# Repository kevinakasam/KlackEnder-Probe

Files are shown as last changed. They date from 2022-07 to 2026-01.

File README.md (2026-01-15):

## KlackEnder Probe

KlackEnder Probe - **Simple, fast and cheap!**

<table>
  <tr>
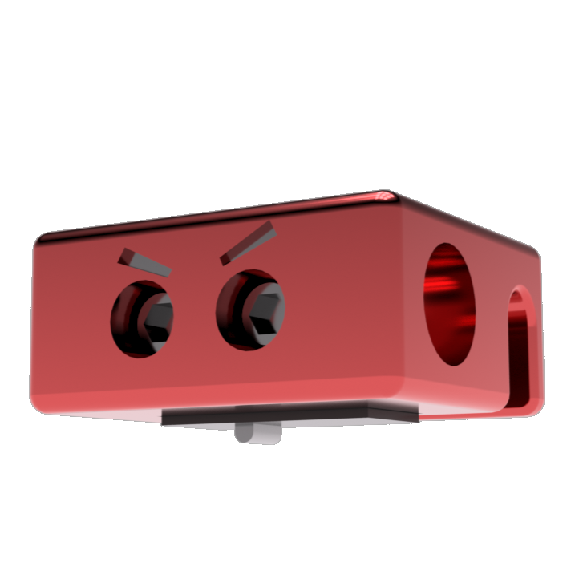
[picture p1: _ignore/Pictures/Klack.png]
    <td> </td>
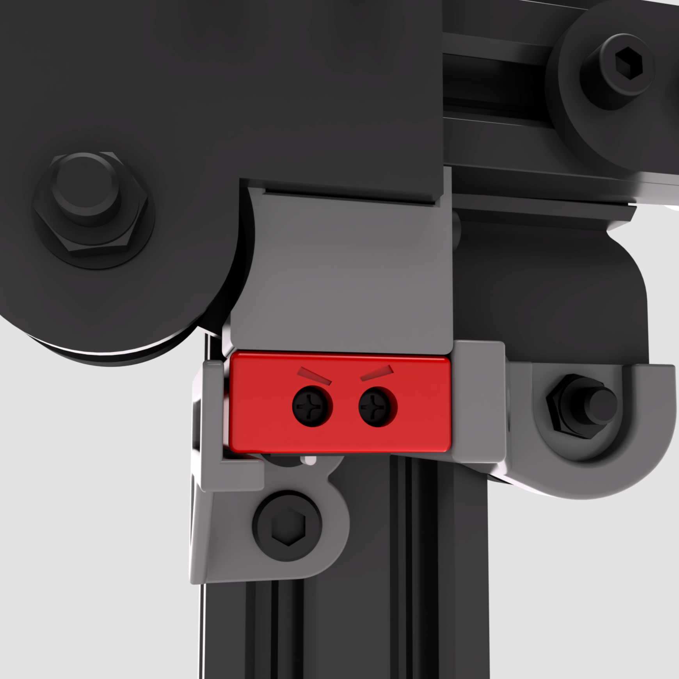
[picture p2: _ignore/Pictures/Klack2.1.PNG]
    <td> </td>
  </tr>
</table>

### What is this about?

Adaptation of the [Klicky](https://github.com/jlas1/Klicky-Probe)/[Quickdraw](https://github.com/Annex-Engineering/Quickdraw_Probe) Probe for the Ender 3 and comparable Creality printers. The probe is compatible with all printers that use the X plate of the Ender 3 and cost of the probe is <10€, of which the switch is the most expensive part.
The probe is compatible with Marlin and Klipper. Both firmwares work with the G29 command, the docking is done automatically by the printer, it couldn't be easier! Both firmwares add a KlackEnder menu to the display that can be used to dock and undock the Probe. The Bed-Mesh can be created via the custom menu, via the default firmware settings or with G29.

### Is it compatible with my printer?

As long as your printer uses a X-Axis plate that's similar to the one of the Ender 3: **YES!***
* You might have to adapt the parts (slightly) if you're not using an Ender 3 or the stock x-plate. See the Basic-Check section to check the basic measurements and see if you printer is compatible. If not and you really struggle with CAD just ping me on my [Discord](https://discord.gg/xqpKrxt9FC) ;)

### Why should I build it?

Well, as with my other mods, the focus is on the best cost-benefit ratio. The KlackEnder is very cheap and very easy to build. No need to pay 40-50€ for a probe that is still affected by heat, takes forever to mesh, and causes a lot of headaches to wire. For the Klack it's: Print - assemble - mount - start printing, that's it. Especially with Klipper, setup couldn't be easier, just use my pre-made macros, copy and paste, hit restart and you're ready for the next print.

#### Quick Overview:

- Compatible with Marlin and Klipper. Easy setup - firmware changes provided.
- 100% automatic probe docking and undocking.
- 100% open source parametric design! With the supported CAD file and instructions, it couldn't be easier to customize the parts to your needs! Even if you've never worked with CAD before, I promise you can customize the parts any way you want!
- Custom menu to control the probe (not for Ender 3 V2 with Jyers GUI).
- The cheapest way to get a fast and very accurate probing ( sample range of 1-2 microsteps (0.000-0.005mm with 16 microsteps)
- Easy to install, no soldering, no complicated wiring
- Works with all pressure surfaces, not affected by heat, no heat soak required

If you have any questions feel free to join the [Discord-Server](https://discord.gg/xqpKrxt9FC).
 
<a href="https://discord.gg/xqpKrxt9FC">
         <img alt="Join" src="https://github.com/kevinakasam/BeltDrivenEnder3/blob/main/_ignore/Pictures/Discord-Logo%2BWordmark-Color.png"
         width=250" >
</a>

<br>

### ❤️ Support my work

All my work is 100% Open-Source and free for everyone to use. But designing and developing all these mods takes a lot of time and effort, so if you appreciate my work and would like to support it and also help cover the costs of gettings the mods perfect, you can use one of the following links. Thanks a lot 🤍

<a href="https://www.buymeacoffee.com/kevinakasam" target="_blank">Buy Me A Coffee</a>


<br>

#### Parametric CAD Design

I always try my best to support a wide range of possible setups so you don't have to deal with CAD. With this design I have gone one step further: Not only does this design support a wide range of setups, but also the CAD is very easy to adapt for anyone, even if you've never worked with CAD before!

**How that? Parametric design!**

Parametric design means that everything is based on variables / parameters which you can easily change. The design itself adapts automatically to the changes you made. This may still sound a bit complicated, but trust me, with the detailed instructions I provide, it couldn't be easier! More about that on my [website](https://kevinakasam.com/lets-adapt-the-cad/).

## Bill of Materials + Instructions

As for my Belt-Mod, you can find all needed Hardware, STLs and instructions on my Website:

<a href="https://kevinakasam.com/klackender/">
         Guide
</a>

### STL-Files / Tolerances
<table>
  <tr>
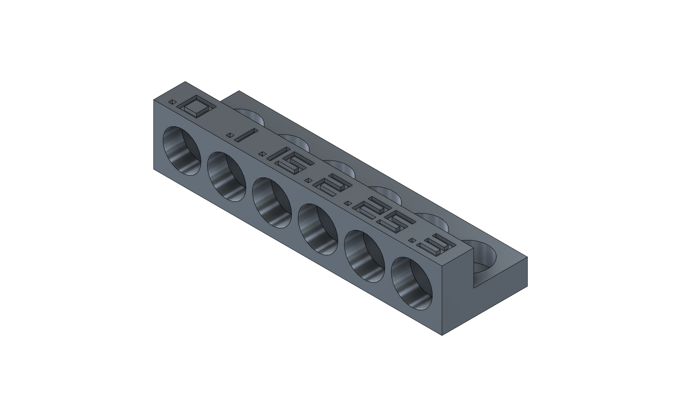
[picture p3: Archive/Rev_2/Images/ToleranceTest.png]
    <td> </td>
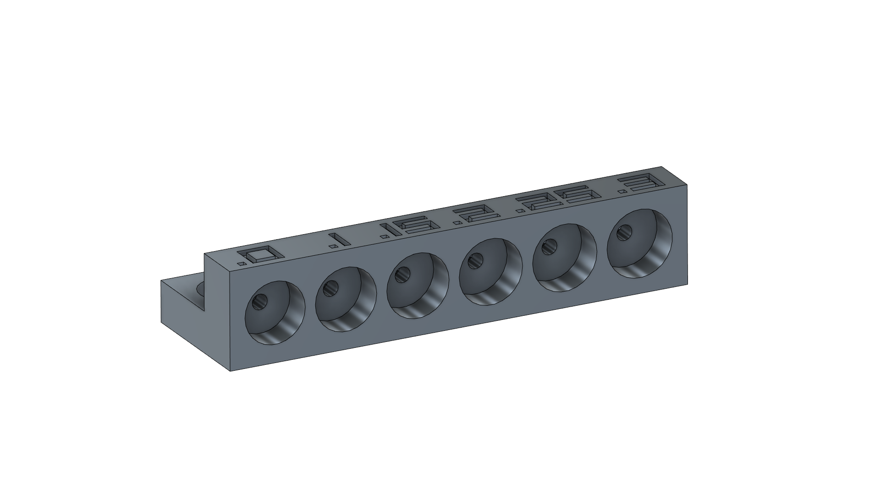
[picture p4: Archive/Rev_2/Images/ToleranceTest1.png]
    <td> </td>
  </tr>
</table>

Some people have contacted me with the problem that the layers split when they insert the magnets. This happens when the magnet is too big for the hole/the hole is too small for the magnet. So either the magnets are a bit bigger than 6mm or your printer prints the holes too small (never use a caliper to measure the magnets!. Only if they are made of plastic!). How the printer prints the holes depends not only on the material (ABS shrinks a bit, while PETG stays fairly constant) but also on the orientation of the holes. Vertical holes are usually a bit smaller than the horizontal ones, the ones that are printed in the walls. This is because these holes are formed by the layers and can never be completely round (the circle is made of 0.2mm (layer height) lines). At the same time, the diameter is strongly influenced by the print settings (speed, acceleration, linear advance/pressure advance, etc.).

However, you may need different tolerances than I do. That is why I have designed a small tolerance test (_thanks to SchlongkyDong for the idea!_). As already described, the tolerances for vertical and horizontal holes can/will differ. Stick a screwdriver through the smaller holes to get your magnets out again.

## Wiring Guide
Since there is no polarity on Switches, it doesn't matter which wire goes where. Just connect the switch to the two marked pins.
In the next chapter about firmware changes you will see where to add the pin.

Wiring for the Rev2 is very easy. Simply unmount/unplug your old z-endstop and connect the probe to the z-endstop port.

## Firmware Guide
The KlackEnder probe works with Marlin and Klipper. This guide only shows you what changes you need to make to the firmware, not how to modify/upload the firmware itself. There are several guides online for different boards and printers.
**You do not have to use the ```Probe In``` or ```Probe Out``` macros.** They're just a nice to have. The printer will do this automatically when you send a ```G29```.

### Klipper

The installation for Klipper is pretty easy. Simply do the changes below and copy the code from the ```KlackEnder.cfg```to your ```printer.cfg```
The ```[gcode_macro G29]``` does the same like the ```[gcode_macro BED_MESH_CALIBRATE]```. I just added this so you can use the G29 command as usual.
#### Changes to the existing config:
```
[stepper_z]
endstop_pin: probe:z_virtual_endstop #if you want to use the Prove as z-endstop (You can unsinstall the stock z endstop then. If not, remove the [homing_override])
#position_endstop: 0 #remove this or uncomment it with a #
position_min: -8 # set a negative value (minimum as the probe z_offset)

[stepper_x]
position_max: 250 #Your printhead have to move all the way to the right to pickup the probe. If your screw collides with the metal plate, simply flip it around.

##Following does not apply for the E3-V2##
[stepper_y]
position_min: READ #most Ender 3 configs have this wrong. Between the nozzle and the bed is a gap of 8mm (Y dimension) when the printer is homed. If not adapt this and the -8 in the Probe_In Makro (-5 for the Ender 3 Pro). 
position_endstop: SAME AS ABOVE

```
#### Config information:

**Add this DRIECTLY to your `printer.cfg` file:**
  ```
##################################
## Add this to your printer.cfg ##
##################################
#####################################################################
# KlackEnder- Settings
#####################################################################
[include KlackEnder.cfg]
# !! Change your Z endstop pin from 'endstop_pin: Pin123' to 'endstop_pin: probe:z_virtual_endstop'
# !! Also add in [stepper_y] 'position_min: -8'. Idk why but most configs have this wrong. For the Stock Ender 3 the homed Y position is -8.

[probe]
pin: ^YOUR_PIN #Change to where you plug your probe in, endstop or probe pin pulled high (^)
z_offset: 0 #Measure per your specific setup. Klipper will NOT save this value if this in not located in printer.cfg
x_offset: 4 # negative = left of the nozzle
y_offset: 21 # negative = in front of of the nozzle
speed: 5.0
lift_speed: 15.0
sample_retract_dist: 1
samples: 2
samples_tolerance_retries: 6

[bed_mesh]
speed: 300
horizontal_move_z: 5 #Positive value equal to z_offset or larger. eg: if z_offset is -2.5 this must be at least 2.5 or larger
mesh_min: 8,30
mesh_max: 223,201
probe_count: 5,5
#zero_reference_position: 117.5, 117.5 #for 235x235 bed. adapt to your bed size if needed. same for mesh min and max above
algorithm: bicubic
fade_start: 1
fade_end: 10
#fade_target:
#   The z position in which fade should converge. When this value is set
#   to a non-zero value it must be within the range of z-values in the mesh.
#   Users that wish to converge to the z homing position should set this to 0.
#   Default is the average z value of the mesh.
split_delta_z: 0.015
#   The amount of Z difference (in mm) along a move that will
#   trigger a split. Default is .025.
move_check_distance: 3
#   The distance (in mm) along a move to check for split_delta_z.
#   This is also the minimum length that a move can be split. Default
#   is 5.0.
mesh_pps: 4,4
#   A comma separated pair of integers (X,Y) defining the number of
#   points per segment to interpolate in the mesh along each axis. A
#   "segment" can be defined as the space between each probed
#   point. The user may enter a single value which will be applied
#   to both axes.  Default is 2,2.
#bicubic_tension: .2
#   When using the bicubic algorithm the tension parameter above
#   may be applied to change the amount of slope interpolated.
#   Larger numbers will increase the amount of slope, which
#   results in more curvature in the mesh. Default is .2.

[homing_override]
set_position_z:0 # Make printer think Z axis is at zero, so we can force a move upwards away from build plate
axes: z #will only call override if x is involved in the homing call
gcode:
    G90
    G1 Z10 F3000 ; move up to prevent accidentally scratching build plate    
    {% if "x" not in (printer.toolhead.homed_axes | lower) %}
        G28 X
    {% endif %}
    {% if "y" not in (printer.toolhead.homed_axes | lower) %}
        G28 Y        #Will only home XY if they are not currently homed
    {% endif %}
    PROBE_OUT
    G1 X113.5 Y96.5 F6000 ; Adjusted for normal klack offsets with a 235x235 bed X: 117.5 - x_offset, Y: 117.5 - y_offset
    G28 Z
    PROBE_IN
	
[screws_tilt_adjust] #Change to your specific printer is needed. Back left screw as referance point and that's where strain relief is is recommended
screw1: 28.5, 181.5
screw1_name: Back left
screw2: 28.5, 11.5
screw2_name: Front left
screw3: 198.5, 11.5
screw3_name: Front right
screw4: 198.5, 181.5
screw4_name: Back right
screw_thread: CW-M4 #Ender 3s use CW-M4 change for your printer if needed
horizontal_move_z: 10
# To calculate the position of your screws:
# Screw Offsets: 32.5mm for ender 3 beds
# Default Klack probe offsets: X: 4, Y: 21
#Back left	
#   X: 0 + screw_x_offset - probe.x_offset	
#   Y: 235 - screw_y_offset - probe.y_offset
#Front left	
#   X: 0 + screw_x_offset - probe.x_offset	
#   Y: 0 + screw_y_offset - probe.y_offset
#Front right 
#   X: 235 - screw_x_offset - probe.x_offset	
#   Y: 0 + screw_y_offset - probe.y_offset
#Back right	
#   X: 235 - screw_x_offset - probe.x_offset	
#   Y: 235 - screw_y_offset - probe.y_offset
# x and y offsets are usually the same. You will have to find info on your printer or measure them yourself
# This can be adapted for three screw bed as well without eny problem. In that case X offset of the third screw would be build volume divided by 2

[gcode_macro SCREWS_TILT_CALCULATE]
rename_existing: _SCREWS_TILT_CALCULATE
gcode:
    G28 ; Should always home before calculation even if already homed
    probe_out
    _SCREWS_TILT_CALCULATE
    probe_in
```
Add this section if building Dual Z. You can quickly comment and uncomment in Klipper by select the whole block and pressing Ctrl+/
```
##Uncomment for Dual Z setups only!! (with independent motors and drivers, not Y splitters nor dual Z port from one driver on board!)##
#[z_tilt]
#z_positions:
#    25,117
#    210,117
	#   A list of X, Y coordinates (one per line; subsequent lines
	#   indented) describing the location of each bed "pivot point". The
	#   "pivot point" is the point where the bed attaches to the given Z
	#   stepper. It is described using nozzle coordinates (the X, Y position
	#   of the nozzle if it could move directly above the point). The
	#   first entry corresponds to stepper_z, the second to stepper_z1,
	#   the third to stepper_z2, etc. This parameter must be provided.
#points:
#    4,96.5
#    219,96.5
	#   A list of X, Y coordinates (one per line; subsequent lines
	#   indented) that should be probed during a Z_TILT_ADJUST command.
	#   Specify coordinates of the nozzle and be sure the probe is above
	#   the bed at the given nozzle coordinates. This parameter must be
	#   provided.
#speed: 100
	#   The speed (in mm/s) of non-probing moves during the calibration.
	#   The default is 50.
#horizontal_move_z: 15
	#   The height (in mm) that the head should be commanded to move to
	#   just prior to starting a probe operation. The default is 5.
#retries: 10
	#   Number of times to retry if the probed points aren't within
	#   tolerance.
#retry_tolerance: 0.01
	#   If retries are enabled then retry if largest and smallest probed
	#   points differ more than retry_tolerance. Note the smallest unit of
	#   change here would be a single step. However if you are probing
	#   more points than steppers then you will likely have a fixed
	#   minimum value for the range of probed points which you can learn
	#   by observing command output.
	
#[gcode_macro Z_TILT_ADJUST] #Uncomment this macro if using dual z with z_tilt
#rename_existing: _Z_TILT_ADJUST
#gcode:
#    PROBE_OUT
#    _Z_TILT_ADJUST
#    PROBE_IN
```
Below are Macros and Screen menu settings to use with Klack. Add them in a seperate cfg called `KlackEnder.cfg`
```
#####################################################################
# KlackEnder- Macros
#####################################################################

[gcode_macro PROBE_OUT]
gcode:
    G90
    G1 X245 F4000
    G4 P300
    G1 Z15
    G1 X0

[gcode_macro PROBE_IN]
gcode:
    G90
    G1 Z20
    G1 X245 F12000
    G1 Y0 ; Check this against your config of [stepper_y] position_min: ...!
    G1 Z0
    G4 P300
    G1 X220 F6000
    G1 Z10
    G1 X0

[gcode_macro BED_MESH_CALIBRATE] #macro with parameter passing
rename_existing: _BED_MESH_CALIBRATE
gcode:
    PROBE_OUT
    _BED_MESH_CALIBRATE {rawparams}
    PROBE_IN

[gcode_macro G29] #reliant on the macro above
gcode:
    BED_MESH_CALIBRATE

[gcode_macro PROBE_CALIBRATE]
rename_existing: _PROBE_CALIBRATE
gcode:
    {% if not 'xyz' in printer.toolhead.homed_axes %}
    G28
    {% endif %}
    PROBE_OUT
    G90
    G1 Z20
    G1 X113.5 Y96.5 F12000 ; Readjust for center of bed adjusted for probe offset
    _PROBE_CALIBRATE
    TESTZ Z=20
    M117 Remove the Klack to continue calibration!

[gcode_macro PROBE_ACCURACY]
rename_existing: _PROBE_ACCURACY
gcode:
    {% if not 'xyz' in printer.toolhead.homed_axes %}
    G28
    {% endif %}
    PROBE_OUT
    G90
    G1 X113.5 Y96.5 F12000 ; Readjust for center of bed adjusted for probe offset
    _PROBE_ACCURACY
    PROBE_IN

#################################################################
#    KlackEnder- Menu - Only if you have a display installed!   #
# Will error if you don't have a display configured in klipper. #
#                       Remove if unneeded                      #
#################################################################

[menu __main]
type: list
name: Main

[menu __main __KlackEnder]
type: list
enable: True
name: KlackEnder

[menu __main __KlackEnder __ProbeOut]
type: command
name: Probe Out
gcode:
    PROBE_OUT

[menu __main __KlackEnder __ProbeIn]
type: command
name: Probe In
gcode:
    PROBE_IN

[menu __main __KlackEnder __AutoBedMesh]
type: command
name: Auto Bed Mesh
gcode:
    G28
    BED_MESH_CALIBRATE
	
[menu __main __KlackEnder __ScrewsTiltCalculate]
type: command
name: Screws Tilt Calculate
gcode:
    SCREWS_TILT_CALCULATE
  ```
### Kalico
If you are running the Kalico fork of Klipper you can use the `dockable_probe` feature in liu of the `probe` section and specific macros. Add to your `printer.cfg`.

```
[dockable_probe]
pin: ^YOUR_PIN #Change to where you plug your probe in, endstop or probe pin pulled high (^)
#z_offset: 0 #Measure per your specific setup
x_offset: 4 # negative = left of the nozzle
y_offset: 21 # negative = in front of of the nozzle
speed: 5.0
lift_speed: 10.0
sample_retract_dist: 2
samples: 3
samples_tolerance: 0.00625
samples_tolerance_retries: 6
#activate_gcode:
#deactivate_gcode:
drop_first_result: False #Make True if you have first probe inconsistancies

# Important Bits: These values may vary from printer to printer#
dock_position: 245,10 #Where the Klack is docked. ~X245 for v-wheel mount. ~X249 for Frank linear rail. Y value for clearance.
approach_position: 245,15 #same as dock_position for Euclid style probes
detach_position: 230,10,2 #Lower gantry to small Z pos to detach the probe
extract_position: 230,10 #Move that take the probe out of the dock
insert_position: 245,10 #same as dock_position for Euclid style probes

#safe_dock_distance :
#safe_position : approach_position
z_hop: 15.0 #This forces the toolhead up if not homed or moves the toolhead up to this value if already homed
restore_toolhead: True
#dock_retries:
auto_attach_detach: True
attach_speed:70
detach_speed:100
travel_speed:150
check_open_attach: True

[bed_mesh]
speed: 300
horizontal_move_z: 5 #Positive value equal to z_offset or larger. eg: if z_offset is -2.5 this must be at least 2.5 or larger
mesh_min: 8,30
mesh_max: 223,201
probe_count: 5,5
#zero_reference_position: 117.5, 117.5 #for 235x235 bed. adapt to your bed size if needed. same for mesh min and max above
algorithm: bicubic
fade_start: 1
fade_end: 10
#fade_target:
#   The z position in which fade should converge. When this value is set
#   to a non-zero value it must be within the range of z-values in the mesh.
#   Users that wish to converge to the z homing position should set this to 0.
#   Default is the average z value of the mesh.
split_delta_z: 0.015
#   The amount of Z difference (in mm) along a move that will
#   trigger a split. Default is .025.
move_check_distance: 3
#   The distance (in mm) along a move to check for split_delta_z.
#   This is also the minimum length that a move can be split. Default
#   is 5.0.
mesh_pps: 4,4
#   A comma separated pair of integers (X,Y) defining the number of
#   points per segment to interpolate in the mesh along each axis. A
#   "segment" can be defined as the space between each probed
#   point. The user may enter a single value which will be applied
#   to both axes.  Default is 2,2.
#bicubic_tension: .2
#   When using the bicubic algorithm the tension parameter above
#   may be applied to change the amount of slope interpolated.
#   Larger numbers will increase the amount of slope, which
#   results in more curvature in the mesh. Default is .2.
```
### Marlin
The installation for Marlin requires some more changes, but I will guide you through this :). These changes are only to get the KlackEnder working correctly. You still need to configure the rest of the options as appropriate for your printer. Support for the KlackEnder and similar probes was only recently added so a current version of Marlin needs to be used. Go to ```https://marlinfw.org/meta/download/``` and download the ```bugfix-2.1.x```. Follow the instructions for downloading, Installing, and configuring VSCode. Before compiling with PlatformIO you will need to setup your config files. Go to ```https://github.com/MarlinFirmware/Configurations/tree/bugfix-2.1.x/config/examples/Creality``` find your Printer/board setup and down load the appropriate Configuration.h & Configuration_adv.h. At this point you will want to go through and make the changes below, once completed you should be good to compile and use your printer. We are working on getting Configuration files posted for common printer combinations as well as .bins uploaded with pre-compiled firmware for common setups.

Marlin will now include a probe deploy and stow option under the motion menu when the Mag_mounted probe is defined.

#### 1. Configuration.h

- Search for ```//#define USE_PROBE_FOR_Z_HOMING``` and uncomment by removing ```//``` before ```#define```
- Search for ```#define PROBE_MANUALLY``` and if not commented out with ```//``` comment it out with ```//```
- If you have plugged your Probe into the Z-Endstop you will need to uncomment ```//#define Z_MIN_PROBE_USES_Z_MIN_ENDSTOP_PIN```
  If you have plugged your Probe into the probe port on your board you don't need to touch this.

- Search for ``` //#define MAG_MOUNTED_PROBE```  uncomment by removing the ```//```
  and change the following lines to
  ```
  #define MAG_MOUNTED_DEPLOY_1 { PROBE_DEPLOY_FEEDRATE, { 245, 114, 20 } }  // Move to side Dock / Attach probe
  #define MAG_MOUNTED_DEPLOY_2 { PROBE_DEPLOY_FEEDRATE, { 200, 114, 020} }  // Move probe off dock
  //#define MAG_MOUNTED_DEPLOY_3 { PROBE_DEPLOY_FEEDRATE, { 245, 114, 20 } }  // lift probe up
  //#define MAG_MOUNTED_DEPLOY_4 { PROBE_DEPLOY_FEEDRATE, {   0,   0,  0 } }  // Extra move if needed
  //#define MAG_MOUNTED_DEPLOY_5 { PROBE_DEPLOY_FEEDRATE, {   0,   0,  0 } }  // Extra move if needed
  #define MAG_MOUNTED_STOW_1   { PROBE_STOW_FEEDRATE,   { 245, 114, 20 } }  // Move to dock
  #define MAG_MOUNTED_STOW_2   { PROBE_STOW_FEEDRATE,   { 245, 114,  0 } }  // Place probe beside remover
  #define MAG_MOUNTED_STOW_3   { PROBE_STOW_FEEDRATE,   { 220, 114,  0 } }  // Side move to remove probe
  #define MAG_MOUNTED_STOW_4   { PROBE_STOW_FEEDRATE,   { 220, 114, 20 } }  // Ensure probe is off
  //#define MAG_MOUNTED_STOW_5   { PROBE_STOW_FEEDRATE,   {   0,   0,  0 } }  // Extra move if needed
  ```
  Probe deploy and stow feed rate can be changed by editing the appropriate lines

- Search for ```NOZZLE_TO_PROBE_OFFSET```  and change
  ```
  #define NOZZLE_TO_PROBE_OFFSET { 10, 10, 0 }

  // Most probes should stay away from the edges of the bed, but
  // with NOZZLE_AS_PROBE this can be negative for a wider probing area.
  #define PROBING_MARGIN 10
  ```

  to

  ```
  #define NOZZLE_TO_PROBE_OFFSET { 8, 21, 1.2 }   //--> set correct offset

  // Most probes should stay away from the edges of the bed, but
  // with NOZZLE_AS_PROBE this can be negative for a wider probing area.
  #define PROBING_MARGIN 15   //--> more clearance to the sides of the bed.
  ```
 
- Search for ```// @section geometry```  and change
  ```
  // The size of the printable area
  #define X_BED_SIZE 200
  #define Y_BED_SIZE 200

  // Travel limits (mm) after homing, corresponding to endstop positions.
  #define X_MIN_POS 0
  #define Y_MIN_POS 0
  #define Z_MIN_POS 0
  #define X_MAX_POS X_BED_SIZE
  #define Y_MAX_POS Y_BED_SIZE
  #define Z_MAX_POS 200
  ```

  For non Ender 3v2's

  ```
  // The size of the printable area
  #define X_BED_SIZE 230    //--> adjust bed size
  #define Y_BED_SIZE 235    //--> adjust bed size

  // Travel limits (mm) after homing, corresponding to endstop positions.
  #define X_MIN_POS 0
  #define Y_MIN_POS -8     //--> adjust endstop position
  #define Z_MIN_POS 0
  #define X_MAX_POS X_BED_SIZE +15     //--> adjust x travel
  #define Y_MAX_POS Y_BED_SIZE
  #define Z_MAX_POS 250     //--> adjust z travel
  ```
  For Ender 3v2's change it to
    ```
  // The size of the printable area
  #define X_BED_SIZE 230    //--> adjust bed size
  #define Y_BED_SIZE 228    //--> adjust bed size

  // Travel limits (mm) after homing, corresponding to endstop positions.
  #define X_MIN_POS 0
  #define Y_MIN_POS 0     //--> adjust endstop position
  #define Z_MIN_POS 0
  #define X_MAX_POS X_BED_SIZE +15     //--> adjust x travel
  #define Y_MAX_POS Y_BED_SIZE
  #define Z_MAX_POS 250     //--> adjust z travel
  ```
 
- Search for ```// @section calibrate```  and change
  ```
  //#define AUTO_BED_LEVELING_3POINT
  //#define AUTO_BED_LEVELING_LINEAR
  //#define AUTO_BED_LEVELING_BILINEAR
  //#define AUTO_BED_LEVELING_UBL
  //#define MESH_BED_LEVELING

  /**
  * Normally G28 leaves leveling disabled on completion. Enable one of
  * these options to restore the prior leveling state or to always enable
  * leveling immediately after G28.
  */
  //#define RESTORE_LEVELING_AFTER_G28
  //#define ENABLE_LEVELING_AFTER_G28
  ```

  to

  ```
  //#define AUTO_BED_LEVELING_3POINT
  //#define AUTO_BED_LEVELING_LINEAR
  //#define AUTO_BED_LEVELING_BILINEAR
  #define AUTO_BED_LEVELING_UBL     //--> Remove //
  //#define MESH_BED_LEVELING

  /**
  * Normally G28 leaves leveling disabled on completion. Enable one of
  * these options to restore the prior leveling state or to always enable
  * leveling immediately after G28.
  */
  #define RESTORE_LEVELING_AFTER_G28    //--> Remove //
  //#define ENABLE_LEVELING_AFTER_G28
  ```
 
- Search for ```Unified Bed Leveling```  
  Change  from ```#define MESH_INSET 1``` to ```#define MESH_INSET 10```
  Change   ```#define GRID_MAX_POINTS_X 10``` to ```#define GRID_MAX_POINTS_X 15```  
  Uncomment  by removing the ```//``` before ```#define UBL_MESH_WIZARD```  
  Uncomment  ```//#define LCD_BED_LEVELING```  
  Uncomment  ```//#define LCD_BED_TRAMMING```  
  Uncomment  ```//#define BED_TRAMMING_USE_PROBE```  
  Uncomment  ```//#define Z_SAFE_HOMING```  
  Uncomment  ```//#define EEPROM_INIT_NOW   // Init EEPROM on first boot after a new build```  

 - In Configuration_adv.H
  Uncomment ```//#define PROBE_OFFSET_WIZARD```

  ## Marlin Setup Before printing
  Go into the menu->Motion->Unified Bed Leveling->UBL Custom Bed Mesh
  set your normal bed temp and hotend temp and then select custom mesh. This will probe all points that can be reached by the probe and then interpolate the rest.
  
  ## Marlin Slicer Start Gcode
  In your slicer Gcode look for a line that says 
  ```G28```
  after that line add in the following two lines
  ```
  G29 L0 ; load mesh saved in slot 0 which is the default slot
  G29 A ; activate bed mesh leveling.
  G29 J ; Probe 3 points and tilt the mesh loaded in slot 0 to match the current bed tilt
  ```

### Rev_1 vs. Rev_2 (and Rev_2.x)

What's the difference between Revision 1 and Revion 2?
                   
The most important difference is the position of the probe. With the Rev2, the probe is attached to the X-axis, which is why the probe can be used as a Z end stop. So no additional port for an end stop is needed and the probe can simply be connected to the old Z endstop port. The renders below show the difference, the upper one is the Rev2. (The Probe mount on the hotendplate is the same for both version)
                   
<table>
  <tr>
    <td><img src="https://github.com/kevinakasam/KlackEnder-Probe/blob/main/Archive/Rev_2/Images/Comp.png" width="450"> </td>
    <td><img src="https://github.com/kevinakasam/KlackEnder-Probe/blob/main/Archive/Rev_2/Images/Comp2.png" width="450"> </td>
  </tr>
</table>

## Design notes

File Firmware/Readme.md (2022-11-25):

Firmware files for the KlackEnder.
See Wiring Guide and Firmware Guide from the main Readme.md for more information.

Marlin instructions are on the main Page!

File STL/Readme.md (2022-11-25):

All parts can be printed without supports. Just print them in the provided orientation.

**Print the tolerance test first!**
All horizontal holes have a tolerance of 0.2mm, all vertical ones have no tolerance. This should fit most printers and give you a tight fit. If the fit isn't right use the provided CAD files to change the tolerance. The f3d file has paramters for that (Check out my [website](https://kevinakasam.com/lets-adapt-the-cad/)). You could also join the discord and I will send you a file with the tolerances you want.

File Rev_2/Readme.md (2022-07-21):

## KlackEnder Probe *Revision 2*

KlackEnder Probe - **Simple, fast and cheap!**
  
Adaptation of the [Klicky](https://github.com/jlas1/Klicky-Probe)/[Quickdraw](https://github.com/Annex-Engineering/Quickdraw_Probe) Probe for the Ender 3 and comparable         Creality printers. The probe is compatible with all printers that use the X plate of the Ender 3. The cost of the probe is <5€, of which the switch is the most expensive part.
The probe is compatible with **Marlin and Klipper**. Both firmwares work with the G29 command, the docking is done automatically by the printer, it couldn't be easier! Both    firmwares add a KlackEnder menu to the display that can be used to dock and undock the Probe. The Bed-Mesh can be created via the custom menu, via the default firmware settings or with G29.

**With the Rev2 you can replace the stock limit switch with the probe. This means you don't need an additional endstop port like for the Rev1.**

### Quick Overview:
- Compatible with Marlin and Klipper. Firmware is provided.
- Automatic docking and undocking of the probe.
- Custom menu to control the probe.
- Cheap way to get fast and accurate probing.
- Easy to install, no soldering.
- Works with all print surfaces
- **Use it as Z Endstop with the Rev2**

Its working very well for me. If you have any questions feel free to join the [Discord-Server](https://discord.gg/xqpKrxt9FC) 
 
<a href="https://discord.gg/xqpKrxt9FC">
         <img alt="Join" src="https://github.com/kevinakasam/BeltDrivenEnder3/blob/main/Pictures/Discord-Logo%2BWordmark-Color.png"
         width=250" >
      </a>

<table>
  <tr>
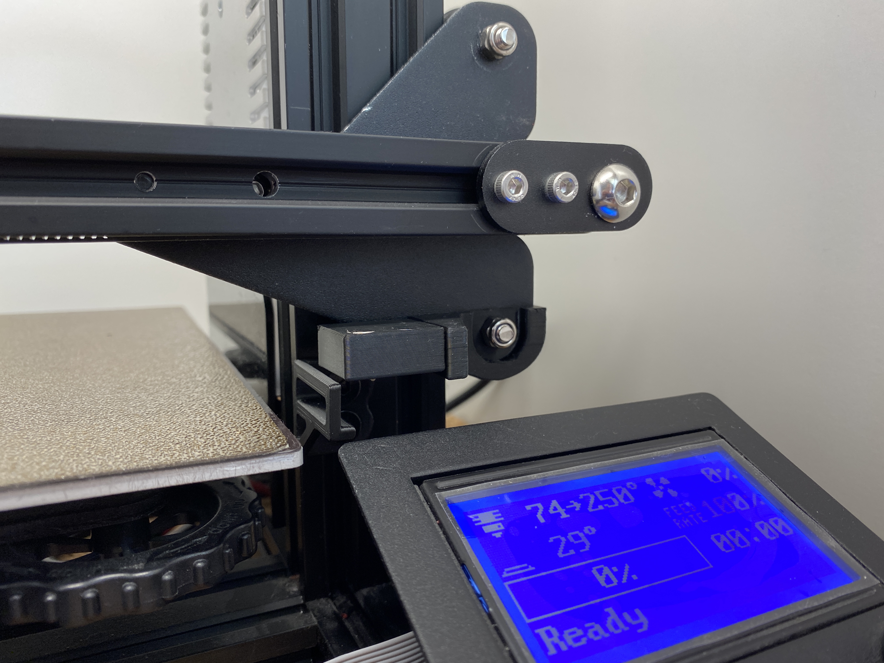
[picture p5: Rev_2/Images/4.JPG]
    <td> </td>
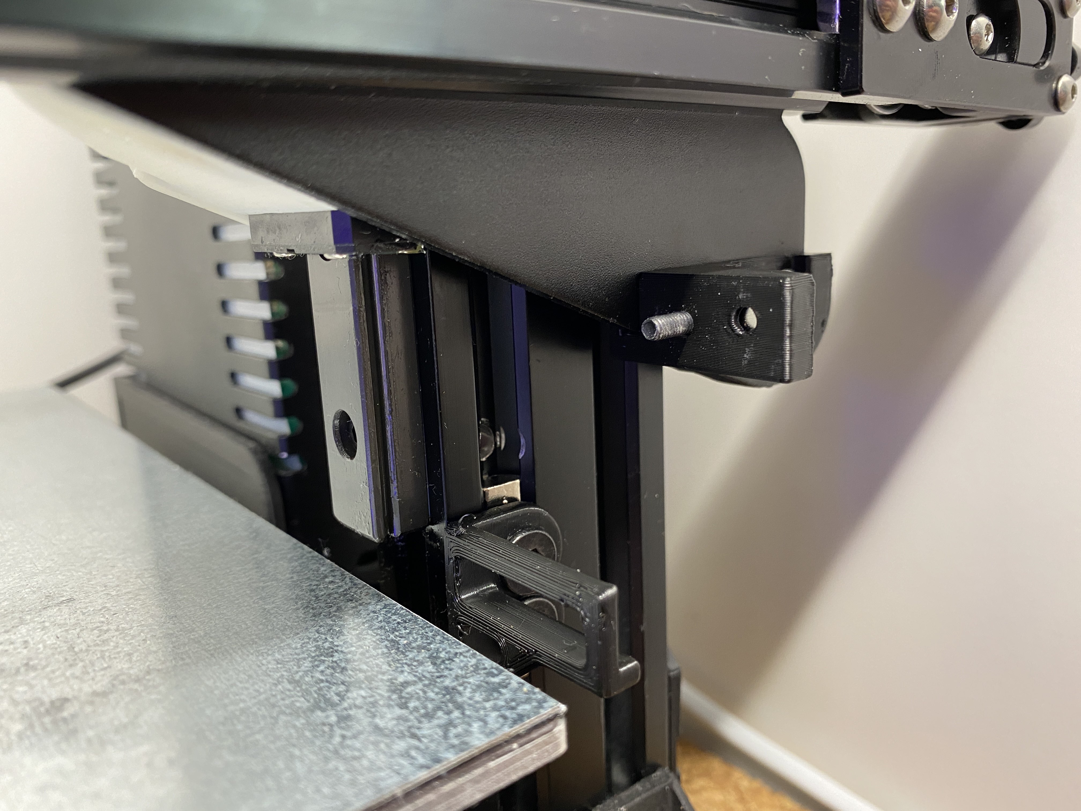
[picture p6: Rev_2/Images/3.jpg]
    <td> </td>
  </tr>
</table>

### BOM - Parts you need:
- 1x OMRON D2F or similar switch
- 6x Magnet 3x6mm 
- 1x M3x12-22mm screw (SHCS or BHCS doesn't matter)
- 2x M5x8mm screw (SHCS or BHCS doesn't matter)
- 2x M5 t-nut
- small zip tie and some cable (you may also need a connector to connect the probe to the mainboard e.g JST XH)
- Users of the Belt Z Mod: 1x M5x45mm screw (SHCS or BHCS doesn't matter) (with the wheels the 40mm screw is just long enough, for the MGN it's too short)
                                                                                                              
## STL-Files / Tolerances
<table>
  <tr>
    <td> </td>
    <td> </td>
  </tr>
</table>

Some people have contacted me with the problem that the layers split when they insert the magnets. This happens when the magnet is too big for the hole/the hole is too small for the magnet. So either the magnets are a bit bigger than 6mm or your printer prints the holes too small (never use a caliper to measure the magnets!. Only if they are made of plastic!). How the printer prints the holes depends not only on the material (ABS shrinks a bit, while PETG stays fairly constant) but also on the orientation of the holes. Vertical holes are usually a bit smaller than the horizontal ones, the ones that are printed in the walls. This is because these holes are formed by the layers and can never be completely round (the circle is made of 0.2mm (layer height) lines). At the same time, the diameter is strongly influenced by the print settings (speed, acceleration, linear advance/pressure advance, etc.).

However, you may need different tolerances than I do. That is why I have designed a small tolerance test (_thanks to SchlongkyDong for the idea!_). As already described, the tolerances for vertical and horizontal holes can/will differ. Stick a screwdriver through the smaller holes to get your magnets out again.

### Parametric Fusion 360 File
There is an f3d file in the [CAD](https://github.com/kevinakasam/KlackEnder-Probe/tree/main/Rev_2/CAD) folder. This file format is for Autodesk Fusion 360, a free CAD program for private users. You can use it to adjust the tolerances if the STL files I provided do not fit.
As described in the tolerance test, there are different tolerances for vertical and horizontal holes. Follow the steps decribes in the [CAD](https://github.com/kevinakasam/KlackEnder-Probe/tree/main/Rev_2/CAD) folder to create your own STL.

## Assembly Guide
                                                                                                               
I will add a Video Guide soon! The assembly is very similar to the Rev1. You will have to insert an additinal magnet into the side of the `Probe_Block.stl`. There also belongs a magnet in the foremost hole of `Probe_Dock.stl` (looking at it when it's mounted). The M3 scew belongs into the rear hole (the thread will stick out of the dock and hold the Proble_Block in place.
                                                                                                               
                                                                                                               
---

## Wiring Guide
Since there is no polarity on Swichtes, it doesn't matter which wire goes where. Just connect the switch to the two marked pins.
In the next chapter about firmware changes you will see where to add the pin.

Wiring for the Rev2 is very easy. Simply unmount/unplug your old z-endstop and connect the probe to the z-endstop port.

## Firmware Guide
The KlackEnder probe works with Marlin and Klipper. This guide only shows you what changes you need to make to the firmware, not how to modify/upload the firmware itself. There are several guides online for different boards and printers.
**You do not have to use the ```Probe In``` or ```Probe Out``` macros.** They're just a nice to have. The printer will do this automatically when you send a ```G29```.

### Klipper

The installation for Klipper is pretty easy. Simply copy the code from the ```KlackEnder.cfg```to your ```printer.cfg```
The ```[gcode_macro G29]``` does the same like the ```[gcode_macro AUTO_BED_MESH]```. I just added this so you can use the G29 commend as usual.

**Don't forgot to edit your probe Pin:**
  ```
  ##################################
## Add this to your printer.cfg ##
################################## 
#####################################################################
#	KlackEnder- Settings
#####################################################################

# !! Change your Z endstop pin from 'endstop_pin: Pin123' to 'endstop_pin: probe:z_virtual_endstop'
# !! Also add in [stepper_y] 'position_min: -8'. Idk why but most configs mave this wrong. For the Stock Ender 3 the homed Y position is -8.

[probe]
pin: ^PC14 #Probe-Stop Connection on Skr Mini Pro V1.2
z_offset: -2 #Measure per your specific setup
x_offset: 8 # negative = left of the nozzle
y_offset: 21 # negative = in front of of the nozzle
speed: 5.0
lift_speed: 15.0
sample_retract_dist: 1
samples: 2
samples_tolerance_retries: 6

##[(7x7)-1] / 2 = 24
##[(5x5)-1] / 2 = 12
[bed_mesh]
speed: 300
horizontal_move_z: 2
mesh_min: 8,30
mesh_max: 223,201
probe_count: 5,5
relative_reference_index: 12
algorithm: bicubic
fade_start: 1
fade_end: 10
#fade_target:
#   The z position in which fade should converge. When this value is set
#   to a non-zero value it must be within the range of z-values in the mesh.
#   Users that wish to converge to the z homing position should set this to 0.
#   Default is the average z value of the mesh.
split_delta_z: 0.015
#   The amount of Z difference (in mm) along a move that will
#   trigger a split. Default is .025.
move_check_distance: 3
#   The distance (in mm) along a move to check for split_delta_z.
#   This is also the minimum length that a move can be split. Default
#   is 5.0.
mesh_pps: 4,4
#   A comma separated pair of integers (X,Y) defining the number of
#   points per segment to interpolate in the mesh along each axis. A
#   "segment" can be defined as the space between each probed
#   point. The user may enter a single value which will be applied
#   to both axes.  Default is 2,2.
#bicubic_tension: .2
#   When using the bicubic algorithm the tension parameter above
#   may be applied to change the amount of slope interpolated.
#   Larger numbers will increase the amount of slope, which
#   results in more curvature in the mesh. Default is .2.

[homing_override]
set_position_z:0 # Make printer think Z axis is at zero, so we can force a move upwards away from build plate
gcode:
    G90
    G1 Z10 F3000 ; move up to prevent accidentally scratching build plate    
    G28 X
    G28 Y
    PROBE_OUT
    G1 X117 Y117 F6000
    G28 Z
    PROBE_IN

##For Dual Z setups only!! (with indipendent motors, no Y splitters or dual Z port on board!)##
[z_tilt]
z_positions:
    0,117
    235,117
#   A list of X, Y coordinates (one per line; subsequent lines
#   indented) describing the location of each bed "pivot point". The
#   "pivot point" is the point where the bed attaches to the given Z
#   stepper. It is described using nozzle coordinates (the X, Y position
#   of the nozzle if it could move directly above the point). The
#   first entry corresponds to stepper_z, the second to stepper_z1,
#   the third to stepper_z2, etc. This parameter must be provided.
points:
    8,96.5
    215,96.5
#   A list of X, Y coordinates (one per line; subsequent lines
#   indented) that should be probed during a Z_TILT_ADJUST command.
#   Specify coordinates of the nozzle and be sure the probe is above
#   the bed at the given nozzle coordinates. This parameter must be
#   provided.
speed: 300
#   The speed (in mm/s) of non-probing moves during the calibration.
#   The default is 50.
horizontal_move_z: 15
#   The height (in mm) that the head should be commanded to move to
#   just prior to starting a probe operation. The default is 5.
retries: 10
#   Number of times to retry if the probed points aren't within
#   tolerance.
retry_tolerance: 0.01
#   If retries are enabled then retry if largest and smallest probed
#   points differ more than retry_tolerance. Note the smallest unit of
#   change here would be a single step. However if you are probing
#   more points than steppers then you will likely have a fixed
#   minimum value for the range of probed points which you can learn
#   by observing command output.

#####################################################################
#	KlackEnder- Macros
#####################################################################

[gcode_macro PROBE_OUT]
gcode:
    G90
    G1 X245 F4000
    G4 P300
    G1 Z15
    G1 X0

[gcode_macro PROBE_IN]
gcode:
    G90
    G1 Z20
    G1 X245 F20000
    G1 Y-8
    G1 Z0
    G4 P300
    G1 X220 F6000
    G1 Z10
    G1 X0

[gcode_macro AUTO_BED_MESH]
gcode:
    PROBE_OUT
    BED_MESH_CALIBRATE
    #G1 Y0 F20000
    PROBE_IN

[gcode_macro G29]
gcode:
    PROBE_OUT
    BED_MESH_CALIBRATE
    #G1 Y0 F20000
    PROBE_IN

[gcode_macro Accuracy_Test]
gcode:
    PROBE_OUT
    G90
    G1 Y120 X120 F20000
    PROBE_ACCURACY
    PROBE_IN

[gcode_macro AUTO_Z_TILT_ADJUST]
gcode:
    PROBE_OUT
    Z_TILT_ADJUST
    PROBE_IN

#####################################################################
#	KlackEnder- Menu
#####################################################################

[menu __main]
type: list
name: Main

[menu __main __KlackEnder]
type: list
enable: True
name: KlackEnder

[menu __main __KlackEnder __ProbeOut]
type: command
name: Probe Out
gcode:
    PROBE_OUT

[menu __main __KlackEnder __ProbeIn]
type: command
name: Probe In
gcode:
    PROBE_IN

[menu __main __KlackEnder __AutoBedMesh]
type: command
name: Auto Bed Mesh
gcode:
    G28
    AUTO_BED_MESH
  ```

### Marlin
The installation for Marlin requires some more changes, but I will guide you through this :). These changes are only to get the KlackEnder working correctly. You still need to configure the rest of the options as appropriate for your printer. Support for the KlackEnder and similar probes was only recently added so a current version of Marlin needs to be used. Go to ```https://marlinfw.org/meta/download/``` and download the ```2.1.x.zip```. Follow the instructions for downloading, Installing, and configuring VSCode. Before compiling with PlatformIO you will need to setup your config files. Go to ```https://github.com/MarlinFirmware/Configurations/tree/bugfix-2.1.x/config/examples/Creality``` find your Printer/board setup and down load the appropriate Configuration.h & Configuration_adv.h. At this point you will want to go through and make the changes below, once completed you should be good to compile and use your printer. We are working on getting Configuration files posted for common printer combinations as well as .bins uploaded with pre-compiled firmeware for common setups.

Marlin will now include a probe deploy and stow option under the motion menu when the Mag_mounted probe is defined.

#### 1. Configuration.h
- Search for ``` #define Z_MIN_PROBE_USES_Z_MIN_ENDSTOP_PIN``` (line 1244) comment out by adding ```//``` before ```#define```

- Search for ```//#define USE_PROBE_FOR_Z_HOMING``` and uncomment by remvoving ```//``` before ```#define```

- Search for ``` //#define MAG_MOUNTED_PROBE``` (line 1349) uncomment by removing the ```//```
  and change lines 1354-1363 to 
  ```
  #define MAG_MOUNTED_DEPLOY_1 { PROBE_DEPLOY_FEEDRATE, { 245, 114, 20 } }  // Move to side Dock / Attach probe
  #define MAG_MOUNTED_DEPLOY_2 { PROBE_DEPLOY_FEEDRATE, { 200, 114, 020} }  // Move probe off dock
  //#define MAG_MOUNTED_DEPLOY_3 { PROBE_DEPLOY_FEEDRATE, { 245, 114, 20 } }  // lift probe up
  //#define MAG_MOUNTED_DEPLOY_4 { PROBE_DEPLOY_FEEDRATE, {   0,   0,  0 } }  // Extra move if needed
  //#define MAG_MOUNTED_DEPLOY_5 { PROBE_DEPLOY_FEEDRATE, {   0,   0,  0 } }  // Extra move if needed
  #define MAG_MOUNTED_STOW_1   { PROBE_STOW_FEEDRATE,   { 245, 114, 20 } }  // Move to dock
  #define MAG_MOUNTED_STOW_2   { PROBE_STOW_FEEDRATE,   { 245, 114,  0 } }  // Place probe beside remover
  #define MAG_MOUNTED_STOW_3   { PROBE_STOW_FEEDRATE,   { 240, 114,  0 } }  // Side move to remove probe
  #define MAG_MOUNTED_STOW_4   { PROBE_STOW_FEEDRATE,   { 240, 114, 20 } }  // Ensure probe is off
  //#define MAG_MOUNTED_STOW_5   { PROBE_STOW_FEEDRATE,   {   0,   0,  0 } }  // Extra move if needed
  ```
  Probe deploy and stow feedrate can be changed by edditing line's 1351-1352

- Search for ```NOZZLE_TO_PROBE_OFFSET``` (line 1453) and change
  ```
  #define NOZZLE_TO_PROBE_OFFSET { 10, 10, 0 }

  // Most probes should stay away from the edges of the bed, but
  // with NOZZLE_AS_PROBE this can be negative for a wider probing area.
  #define PROBING_MARGIN 10
  ```

  to 

  ```
  #define NOZZLE_TO_PROBE_OFFSET { 8, 21, 1.2 }   --> set correct offset

  // Most probes should stay away from the edges of the bed, but
  // with NOZZLE_AS_PROBE this can be negative for a wider probing area.
  #define PROBING_MARGIN 15   --> more clearance to the sides of the bed.
  ```
  
- Search for ```// @section machine``` (line 1661) and change
  ```
  // The size of the printable area
  #define X_BED_SIZE 200
  #define Y_BED_SIZE 200

  // Travel limits (mm) after homing, corresponding to endstop positions.
  #define X_MIN_POS 0
  #define Y_MIN_POS 0
  #define Z_MIN_POS 0
  #define X_MAX_POS X_BED_SIZE
  #define Y_MAX_POS Y_BED_SIZE
  #define Z_MAX_POS 200
  ```

  to 

  ```
  // The size of the printable area
  #define X_BED_SIZE 230    --> adjust bed size
  #define Y_BED_SIZE 235    --> adjust bed size

  // Travel limits (mm) after homing, corresponding to endstop positions.
  #define X_MIN_POS 0
  #define Y_MIN_POS -8      --> adjust endstop position
  #define Z_MIN_POS 0
  #define X_MAX_POS +15     --> adjust x travel
  #define Y_MAX_POS Y_BED_SIZE
  #define Z_MAX_POS 250     --> adjust z travel
  ```
  
- Search for ```// @section calibrate``` (line 1806) and change
  ```
  //#define AUTO_BED_LEVELING_3POINT
  //#define AUTO_BED_LEVELING_LINEAR
  //#define AUTO_BED_LEVELING_BILINEAR
  //#define AUTO_BED_LEVELING_UBL
  //#define MESH_BED_LEVELING

  /**
  * Normally G28 leaves leveling disabled on completion. Enable one of
  * these options to restore the prior leveling state or to always enable
  * leveling immediately after G28.
  */
  //#define RESTORE_LEVELING_AFTER_G28
  //#define ENABLE_LEVELING_AFTER_G28
  ```

  to 

  ```
  //#define AUTO_BED_LEVELING_3POINT
  //#define AUTO_BED_LEVELING_LINEAR
  //#define AUTO_BED_LEVELING_BILINEAR
  #define AUTO_BED_LEVELING_UBL     --> Remove //
  //#define MESH_BED_LEVELING

  /**
  * Normally G28 leaves leveling disabled on completion. Enable one of
  * these options to restore the prior leveling state or to always enable
  * leveling immediately after G28.
  */
  #define RESTORE_LEVELING_AFTER_G28    --> Remove //
  //#define ENABLE_LEVELING_AFTER_G28
  ```
  
- Search for ```Unified Bed Leveling``` line(1937)
  Change line 1942 from ```#define MESH_INSET 1```
  to ```#define MESH_INSET 10```
  
  Change line 1943 from ```#define GRID_MAX_POINTS_X 10```  
  to ```#define GRID_MAX_POINTS_X 15```  
  Uncomment line 1954 by removing the ```//``` before ```#define UBL_MESH_WIZARD```  
  Uncomment line 1974 ```//#define LCD_BED_LEVELING```  
  Uncomment Line 1983 ```//#define LCD_BED_TRAMMING```  
  Uncomment Line 1990 ```//#define BED_TRAMMING_USE_PROBE```  
  Uncomment Line 2048 ```//#define Z_SAFE_HOMING```
  Uncomment Line 2138 ```//#define EEPROM_INIT_NOW   // Init EEPROM on first boot after a new build```

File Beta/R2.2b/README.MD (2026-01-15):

Klack R2.2 Beta notes:

Overview:
- New smaller probe block and dock changes!
- Hexagonal holes for the magnets!
- No need to clip the middle lead anymore and leads bend down under the magnets in the block.

BoM Changes:
- No longer need the M3x12-16mm screw for teh dock.

Offset Changes:
- X: Stays the same
- Y: Subtract 2mm

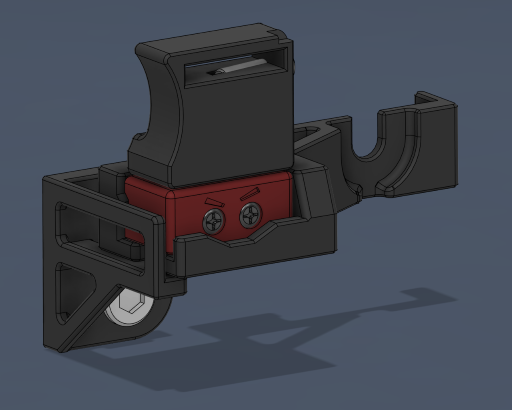
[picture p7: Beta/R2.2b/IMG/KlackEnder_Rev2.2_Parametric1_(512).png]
Klack Rev2.2


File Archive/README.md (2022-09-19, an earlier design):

## KlackEnder Probe

KlackEnder Probe - **Simple, fast and cheap!**
  
Adaptation of the [Klicky](https://github.com/jlas1/Klicky-Probe)/[Quickdraw](https://github.com/Annex-Engineering/Quickdraw_Probe) Probe for the Ender 3 and comparable         Creality printers. The probe is compatible with all printers that use the X plate of the Ender 3. The cost of the probe is <5€, of which the switch is the most expensive part.
The probe is compatible with **Marlin and Klipper**. Both firmwares work with the G29 command, the docking is done automatically by the printer, it couldn't be easier! Both    firmwares add a KlackEnder menu to the display that can be used to dock and undock the Probe. The Bed-Mesh can be created via the custom menu, via the default formware settings or with G29.

I recommend to use the Rev2!

### Quick Overview:
- Compatible with Marlin and Klipper. Firmware is provided.
- Automatic docking and undocking of the probe.
- Custom menu to control the probe.
- Cheap way to get fast and accurate probing.
- Easy to install, no soldering.
- Works with all print surfaces
- **Use it as Z Endstop with the Rev2**

Its working very well for me. If you have any questions feel free to join the [Discord-Server](https://discord.gg/xqpKrxt9FC) 
 
<a href="https://discord.gg/xqpKrxt9FC">
         <img alt="Join" src="https://github.com/kevinakasam/BeltDrivenEnder3/blob/main/_ignore/Pictures/Discord-Logo%2BWordmark-Color.png"
         width=250" >
</a>

### Rev_1 vs. Rev_2
What's the difference between Revision 1 and Revion 2?
                   
The most important difference is the position of the probe. With the Rev2, the probe is attached to the X-axis, which is why the probe can be used as a Z end stop. So no additional port for an end stop is needed and the probe can simply be connected to the old Z endstop port. The renders below show the difference, the upper one is the Rev2. (The Probe mount on the hotendplate is the same for both version)
                   
<table>
  <tr>
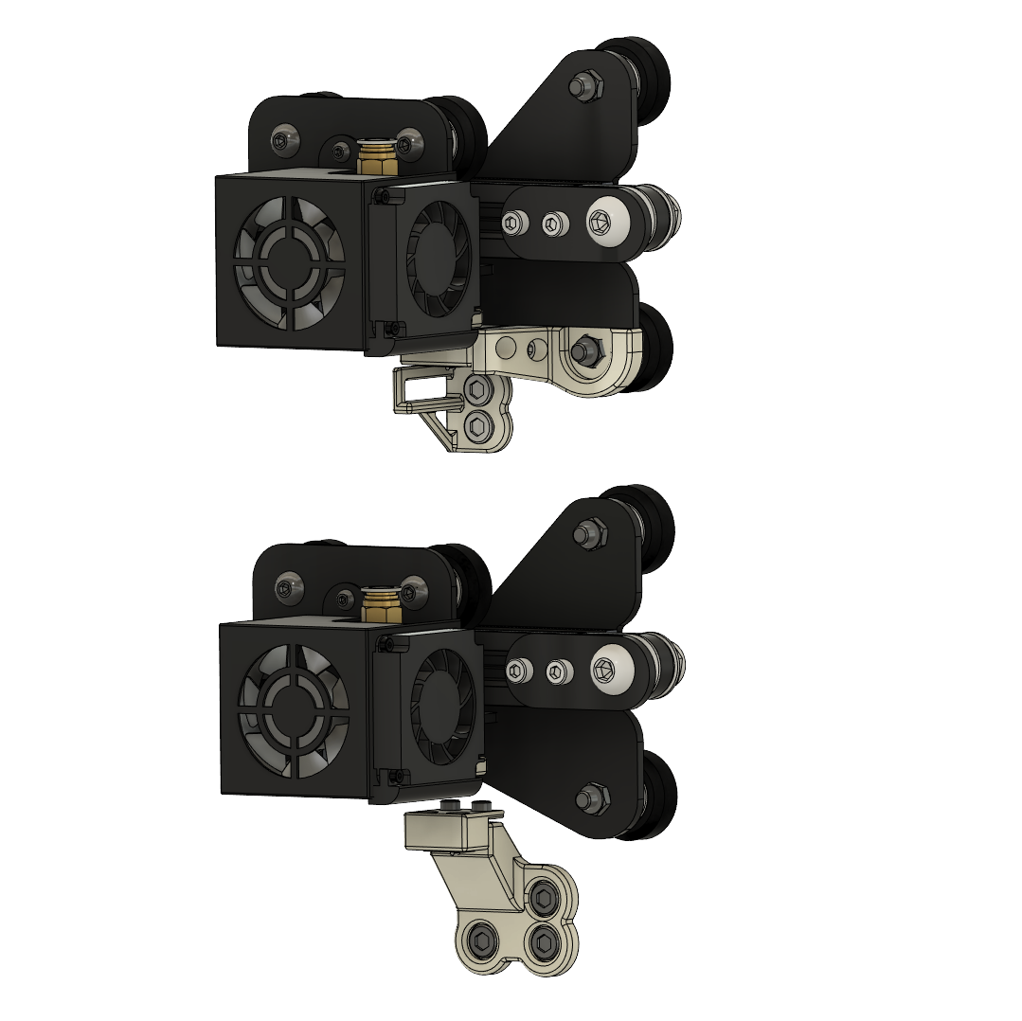
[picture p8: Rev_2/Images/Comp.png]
    <td> </td>
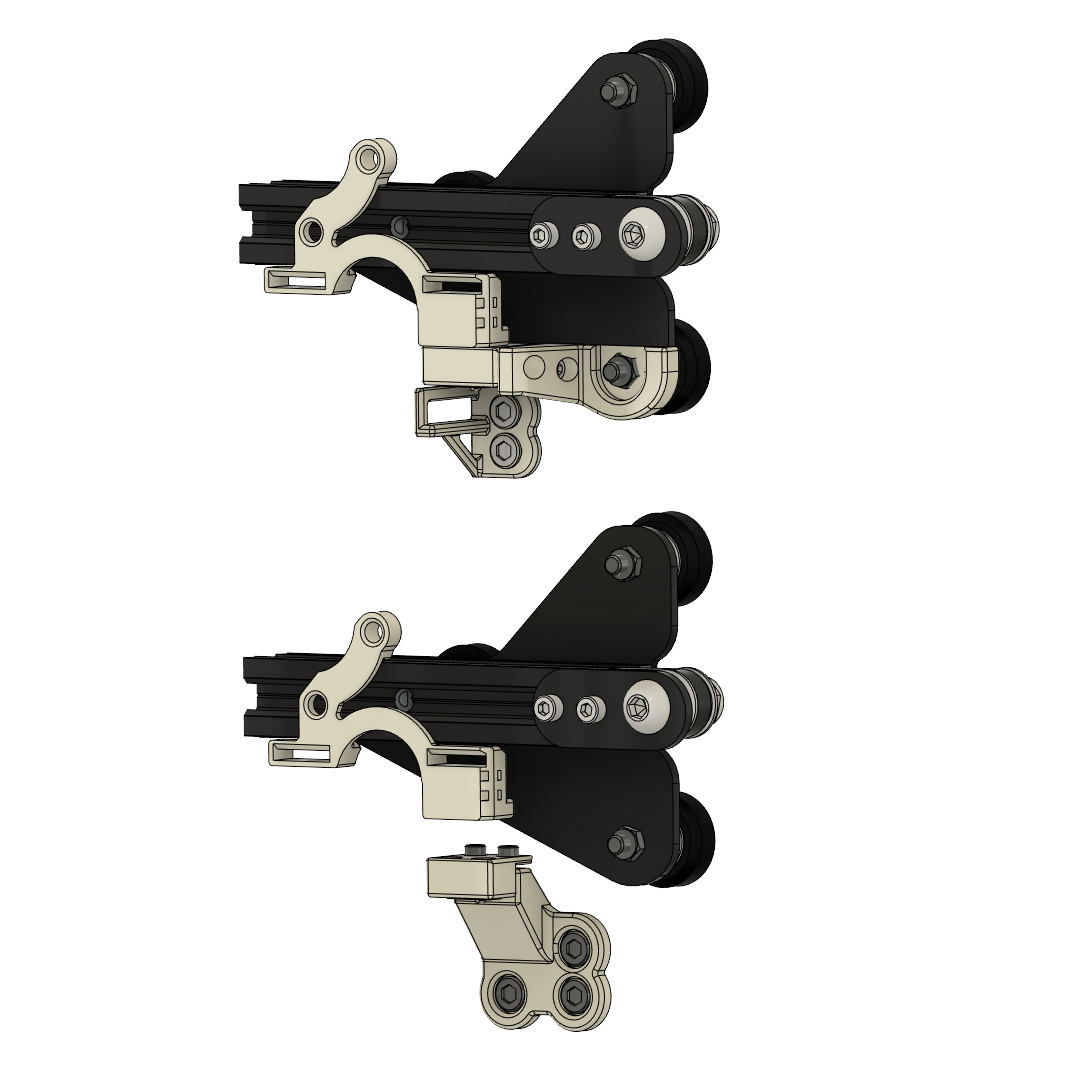
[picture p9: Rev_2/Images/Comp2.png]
    <td> </td>
  </tr>
</table>

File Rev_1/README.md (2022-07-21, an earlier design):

## KlackEnder Probe *Revision 1*

KlackEnder Probe - **Simple, fast and cheap!**
  
Adaptation of the [Klicky](https://github.com/jlas1/Klicky-Probe)/[Quickdraw](https://github.com/Annex-Engineering/Quickdraw_Probe) Probe for the Ender 3 and comparable         Creality printers. The probe is compatible with all printers that use the X plate of the Ender 3. The cost of the probe is <5€, of which the switch is the most expensive part.
The probe is compatible with **Marlin and Klipper**. Both firmwares work with the G29 command, the docking is done automatically by the printer, it couldn't be easier! Both    firmwares add a KlackEnder menu to the display that can be used to dock and undock the Probe. The Bed-Mesh can be created via the custom menu, via the default formware settings or with G29. **Important note: You have to set the offset to the z limit switch, not to the probe! The printer calculates the first layer from the z endstops position and the probed mesh!**

### Quick Overview:
- Compatible with Marlin and Klipper. Firmware is provided.
- Automatic docking and undocking of the probe.
- Custom menu to control the probe.
- Cheap way to get fast and accurate probing.
- Easy to install, no soldering.
- Works with all print surfaces

Its working very well for me. If you have any questions feel free to join the [Discord-Server](https://discord.gg/xqpKrxt9FC) 
 
<a href="https://discord.gg/xqpKrxt9FC">
         <img alt="Join" src="https://github.com/kevinakasam/BeltDrivenEnder3/blob/main/Pictures/Discord-Logo%2BWordmark-Color.png"
         width=250" >
      </a>

<table>
  <tr>
    <td> </td>
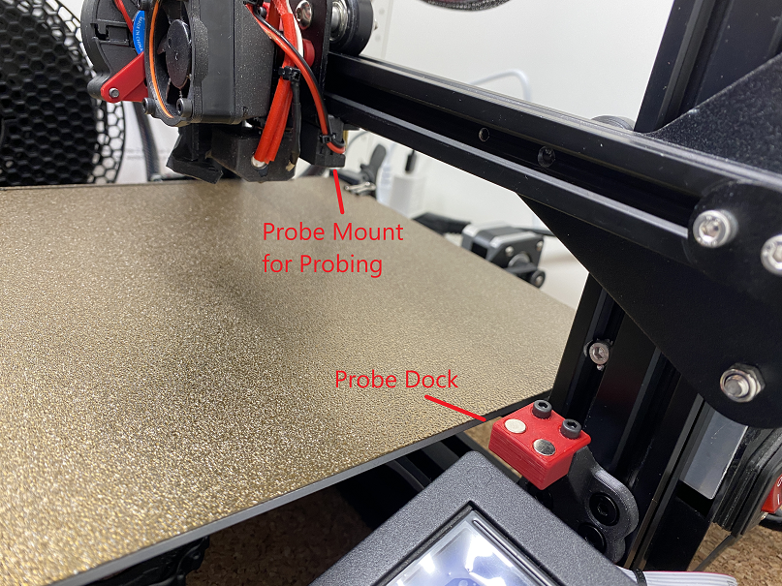
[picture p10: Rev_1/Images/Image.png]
    <td> </td>
  </tr>
</table>

### BOM - Parts you need:
- 1x OMRON D2F or similar switch
- 4x Magnet 3x6mm 
- 2x M3x8mm screw (SHCS or BHCS doesn't matter)
- 3x M5x8mm screw (SHCS or BHCS doesn't matter)
- 3x M5 t-nut
- small zip tie and some cable (you may also need a connector to connect the probe to the mainboard e.g JST XH)

## Assembly Guide
I made a short video about the assembly and installation of the probe.

Wiring and firmware changes are described at the bottom of the page.

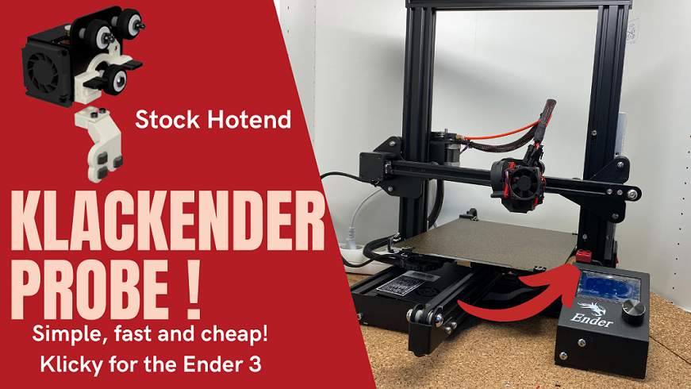
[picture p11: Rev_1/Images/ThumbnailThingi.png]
Video Guide (https://youtu.be/zpy08KOuiJg "Click to Watch!")


---

## Wiring Guide
Since there is no polarity on Swichtes, it doesn't matter which wire goes where. Just connect the switch to the two marked pins.
In the next chapter about firmware changes you will see where to add the pin.

**If you want me to add more mainboards feel free to contact me on Discord: kevinakasam#2097**

#### Stock Ender 3+Pro / Creality3D V1.1.x
- Currently I do not know how to connect an additional endstop to the stock Creality3D V1.1.x Mainboard
       
    

- Image source [3D-Druck-Community](https://www.3d-druck-community.de/showthread.php?tid=23449)
- Pin for Firmware: 

#### Ender 3 V2 / Silent Board V4.2.7 (or all Creality3D V4.x.x)
- Connect the probe to the two marked pins (G and Out). This pins would be also used to connect a BL-Touch.
       
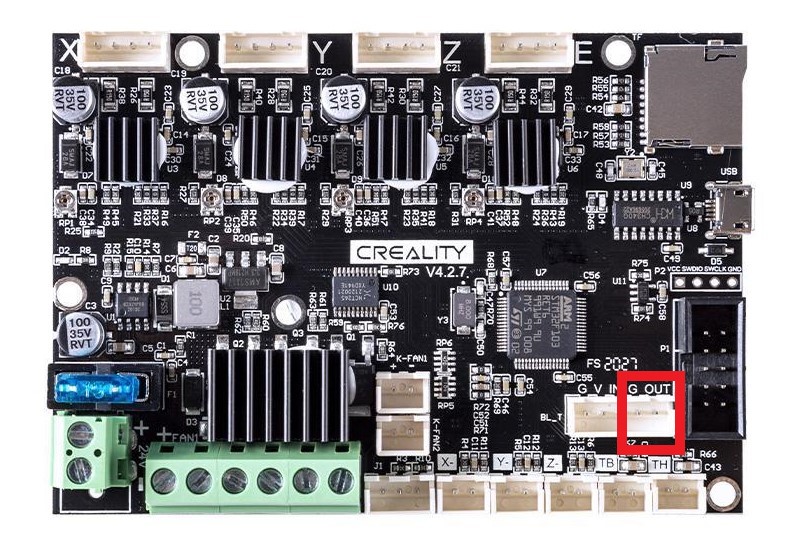
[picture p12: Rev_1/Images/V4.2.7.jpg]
    

- Image source [Creality3D](https://creality3d.shop/products/creality3d-upgrade-silent-4-2-7-1-1-5-mainboard-for-ender-3-ender-3-pro-ender-5-3d-printer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)
- Pin for Firmware: PB1

#### BIGTREETECH SKR Mini E3 V1.x
- Connect the probe to the two marked pins (Probe port).
       
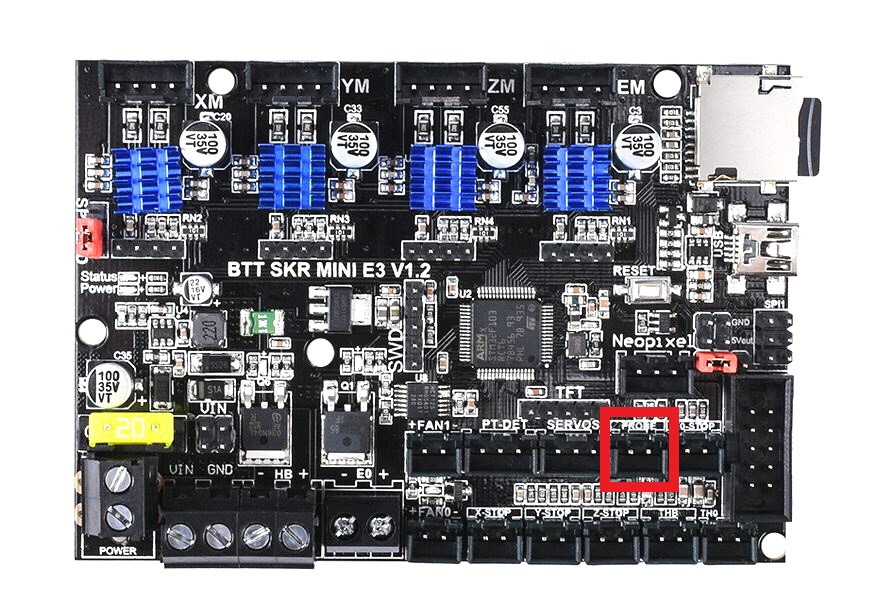
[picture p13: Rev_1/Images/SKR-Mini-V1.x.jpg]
    

- Image source [printertec](https://www.printertec.ch/elektronik/arduino/335/skr-mini-e3-v1.2-control-board-32-bit-cpu-32bit-board-fuer-ender-cr-10)
- Pin for Firmware: PC14

#### BIGTREETECH SKR Mini E3 V2.x
- Connect the probe to the two marked pins (Part of the BL-Touch port).
       
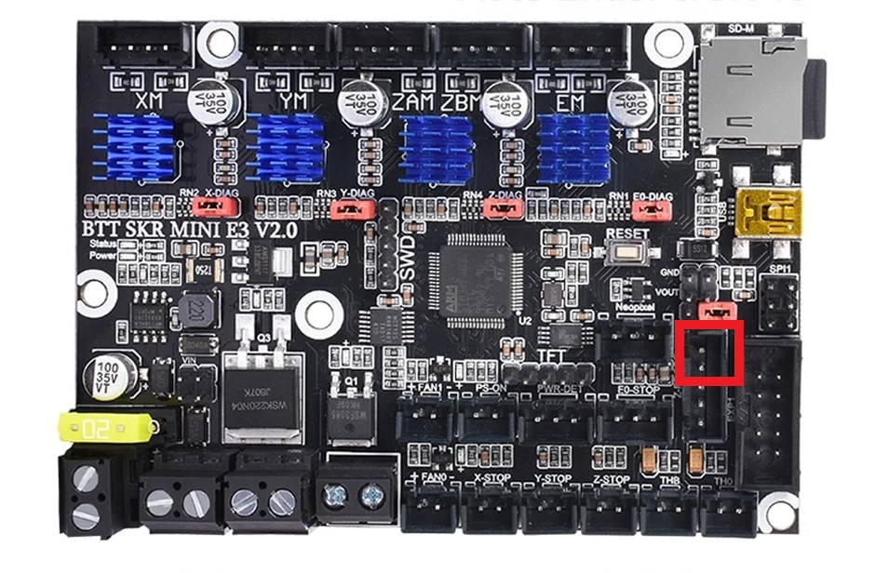
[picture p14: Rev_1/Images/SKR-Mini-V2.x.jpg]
    

- Image source [BIGTREETECH](https://ae01.alicdn.com/kf/H27db29b02f354dc3abb6e36905bc45cdm/BIGTREETECH-BTT-SKR-MINI-E3-V2-Control-Board-32bit-Mit-TMC2209-3D-Drucker-Teile-Motherboard-F.jpg_Q90.j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)
- Pin for Firmware: PC14

#### BIGTREETECH SKR Mini E3 V3.x
- Connect the probe to the two marked pins (Probe port).
       
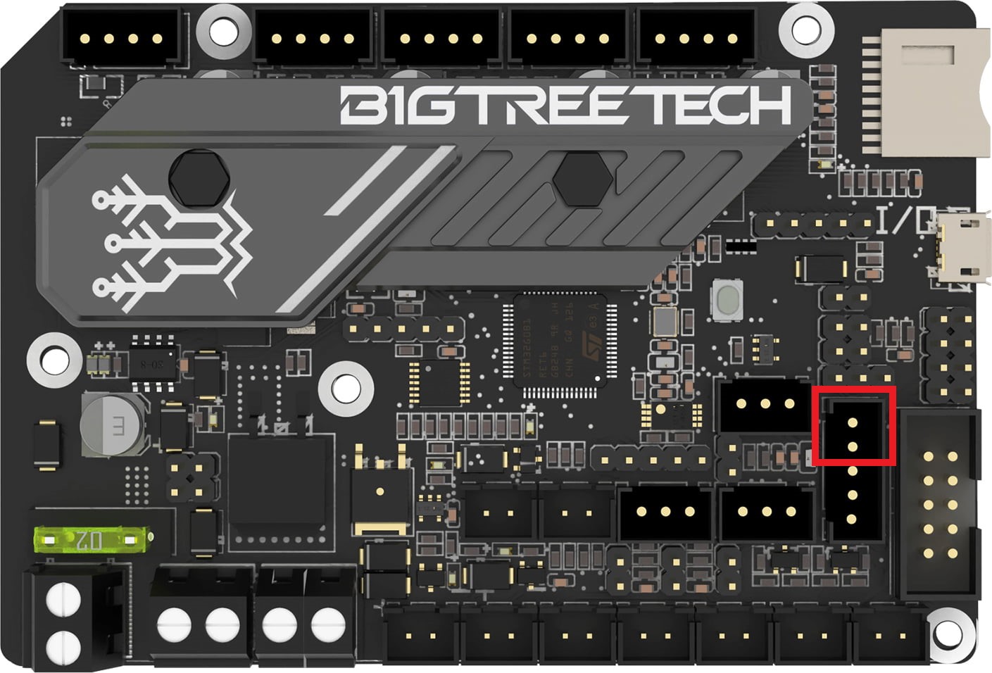
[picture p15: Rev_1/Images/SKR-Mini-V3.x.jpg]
    

- Image source [3djake](https://www.3djake.de/bigtreetech/skr-mini-e3)
- Pin for Firmware: PC14

## Firmware Guide
The KlackEnder probe works with Marlin and Klipper. This guide only shows you what changes you need to make to the firmware, not how to modify/upload the firmware itself. There are several guides online for different boards and printers.
**You do not have to use the ```Probe In``` or ```Probe Out``` macros.** They're just a nice to have. The printer will do this automatically when you send a ```G29```.

**Important note: You have to set the offset to the z limit switch, not to the probe! The printer calculates the first layer from the z endstops position and the probed mesh!**

### Klipper

The installation for Klipper is pretty easy. Simply copy the code from the ```KlackEnder.cfg```to your ```printer.cfg```
The ```[gcode_macro G29]``` does the same like the ```[gcode_macro AUTO_BED_MESH]```. I just added this so you can use the G29 commend as usual.

**Don't forgot to edit your probe Pin:**
  ```
  #####################################################################
  #	KlackEnder- Settings
  #####################################################################

  [probe]
  pin: ^PC14 #Probe-Stop Connection on Skr Mini E3 DIP. Change this if needed!
  z_offset: 0 #Measure per your specific setup
  x_offset: 8 # negative = left of the nozzle
  y_offset: 21 # negative = in front of of the nozzle
  speed: 5.0
  lift_speed: 15.0
  sample_retract_dist: 1
  samples: 2
  samples_tolerance_retries: 6

  ##[(7x7)-1] / 2 = 24
  ##[(5x5)-1] / 2 = 12
  [bed_mesh]
  speed: 300
  horizontal_move_z: 2
  mesh_min: 8,30
  mesh_max: 223,201
  probe_count: 5,5
  relative_reference_index: 12
  algorithm: bicubic
  fade_start: 1
  fade_end: 10
  #fade_target:
  #   The z position in which fade should converge. When this value is set
  #   to a non-zero value it must be within the range of z-values in the mesh.
  #   Users that wish to converge to the z homing position should set this to 0.
  #   Default is the average z value of the mesh.
  split_delta_z: 0.015
  #   The amount of Z difference (in mm) along a move that will
  #   trigger a split. Default is .025.
  move_check_distance: 3
  #   The distance (in mm) along a move to check for split_delta_z.
  #   This is also the minimum length that a move can be split. Default
  #   is 5.0.
  mesh_pps: 4,4
  #   A comma separated pair of integers (X,Y) defining the number of
  #   points per segment to interpolate in the mesh along each axis. A
  #   "segment" can be defined as the space between each probed
  #   point. The user may enter a single value which will be applied
  #   to both axes.  Default is 2,2.
  #bicubic_tension: .2
  #   When using the bicubic algorithm the tension parameter above
  #   may be applied to change the amount of slope interpolated.
  #   Larger numbers will increase the amount of slope, which
  #   results in more curvature in the mesh. Default is .2.

  #####################################################################
  #	KlackEnder- Macros
  #####################################################################

  [gcode_macro PROBE_OUT]
  gcode:
      G90
      G1 Z5
      G1 X245 F20000
      G1 Z0
      G4 P300
      G1 Z20
      G1 X0

  [gcode_macro PROBE_IN]
  gcode:
      G90
      G1 Z20
      G1 X245 F20000
      G1 Z0
      G4 P300
      G1 X240 F1000
      G1 Z5
      G4 P300
      G1 X0 F20000
      G1 Z0

  [gcode_macro AUTO_BED_MESH]
  gcode:
      PROBE_OUT
      BED_MESH_CALIBRATE
      G1 Y0 F20000
      PROBE_IN

  [gcode_macro G29]
  gcode:
      PROBE_OUT
      BED_MESH_CALIBRATE
      G1 Y0 F20000
      PROBE_IN

  #####################################################################
  #	KlackEnder- Menu
  #####################################################################

  [menu __main]
  type: list
  name: Main

  [menu __main __KlackEnder]
  type: list
  enable: True
  name: KlackEnder

  [menu __main __KlackEnder __ProbeOut]
  type: command
  name: Probe Out
  gcode:
      PROBE_OUT

  [menu __main __KlackEnder __ProbeIn]
  type: command
  name: Probe In
  gcode:
      PROBE_IN

  [menu __main __KlackEnder __AutoBedMesh]
  type: command
  name: Auto Bed Mesh
  gcode:
      G28
      AUTO_BED_MESH
  ```

### Marlin
### Marlin
The installation for Marlin requires some more changes, but I will guide you through this :). These changes are only to get the KlackEnder working correctly. You still need to configure the rest of the options as appropriate for your printer. Support for the KlackEnder and similar probes was only recently added so a current version of Marlin needs to be used. Go to ```https://marlinfw.org/meta/download/``` and download the ```2.1.x.zip```. Follow the instructions for downloading, Installing, and configuring VSCode. Before compiling with PlatformIO you will need to setup your config files. Go to ```https://github.com/MarlinFirmware/Configurations/tree/bugfix-2.1.x/config/examples/Creality``` find your Printer/board setup and down load the appropriate Configuration.h & Configuration_adv.h. At this point you will want to go through and make the changes below, once completed you should be good to compile and use your printer. We are working on getting Configuration files posted for common printer combinations as well as .bins uploaded.

Marlin will now include a probe deploy and stow option under the motion menu when the Mag_mounted probe is defined.

#### 1. Configuration.h
- Search for ``` #define Z_MIN_PROBE_USES_Z_MIN_ENDSTOP_PIN``` (line 1244) comment out by adding ```//``` before ```#define```

- Search for ``` //#define MAG_MOUNTED_PROBE``` (line 1349) uncomment by removing the ```//```
  and change lines 1354-1363 to 
  ```
  #define MAG_MOUNTED_DEPLOY_1 { PROBE_DEPLOY_FEEDRATE, { 245, 114, 30 } }  // Move to side Dock
  #define MAG_MOUNTED_DEPLOY_2 { PROBE_DEPLOY_FEEDRATE, { 245, 114, 0 } }  // Move down to probe / Attach probe
  #define MAG_MOUNTED_DEPLOY_3 { PROBE_DEPLOY_FEEDRATE, { 245, 114, 20 } }  // lift probe up
  //#define MAG_MOUNTED_DEPLOY_4 { PROBE_DEPLOY_FEEDRATE, {   0,   0,  0 } }  // Extra move if needed
  //#define MAG_MOUNTED_DEPLOY_5 { PROBE_DEPLOY_FEEDRATE, {   0,   0,  0 } }  // Extra move if needed
  #define MAG_MOUNTED_STOW_1   { PROBE_STOW_FEEDRATE,   { 245, 114, 20 } }  // Move to dock
  #define MAG_MOUNTED_STOW_2   { PROBE_STOW_FEEDRATE,   { 245, 114,  0 } }  // Place probe on dock
  #define MAG_MOUNTED_STOW_3   { PROBE_STOW_FEEDRATE,   { 240, 114,  0 } }  // Side move to remove probe
  #define MAG_MOUNTED_STOW_4   { PROBE_STOW_FEEDRATE,   { 240, 114, 20 } }  // Side move to remove probe
  //#define MAG_MOUNTED_STOW_5   { PROBE_STOW_FEEDRATE,   {   0,   0,  0 } }  // Extra move if needed
  ```
  Probe deploy and stow feedrate can be changed by edditing line's 1351-1352

- Search for ```NOZZLE_TO_PROBE_OFFSET``` (line 1453) and change
  ```
  #define NOZZLE_TO_PROBE_OFFSET { 10, 10, 0 }

  // Most probes should stay away from the edges of the bed, but
  // with NOZZLE_AS_PROBE this can be negative for a wider probing area.
  #define PROBING_MARGIN 10
  ```

  to 

  ```
  #define NOZZLE_TO_PROBE_OFFSET { 8, 21, 1.2 }   --> set correct offset

  // Most probes should stay away from the edges of the bed, but
  // with NOZZLE_AS_PROBE this can be negative for a wider probing area.
  #define PROBING_MARGIN 15   --> more clearance to the sides of the bed.
  ```
  
- Search for ```// @section machine``` (line 1661) and change
  ```
  // The size of the printable area
  #define X_BED_SIZE 200
  #define Y_BED_SIZE 200

  // Travel limits (mm) after homing, corresponding to endstop positions.
  #define X_MIN_POS 0
  #define Y_MIN_POS 0
  #define Z_MIN_POS 0
  #define X_MAX_POS X_BED_SIZE
  #define Y_MAX_POS Y_BED_SIZE
  #define Z_MAX_POS 200
  ```

  to 

  ```
  // The size of the printable area
  #define X_BED_SIZE 230    --> adjust bed size
  #define Y_BED_SIZE 235    --> adjust bed size

  // Travel limits (mm) after homing, corresponding to endstop positions.
  #define X_MIN_POS 0
  #define Y_MIN_POS -8      --> adjust endstop position
  #define Z_MIN_POS 0
  #define X_MAX_POS +15     --> adjust x travel
  #define Y_MAX_POS Y_BED_SIZE
  #define Z_MAX_POS 250     --> adjust z travel
  ```
  
- Search for ```// @section calibrate``` (line 1806) and change
  ```
  //#define AUTO_BED_LEVELING_3POINT
  //#define AUTO_BED_LEVELING_LINEAR
  //#define AUTO_BED_LEVELING_BILINEAR
  //#define AUTO_BED_LEVELING_UBL
  //#define MESH_BED_LEVELING

  /**
  * Normally G28 leaves leveling disabled on completion. Enable one of
  * these options to restore the prior leveling state or to always enable
  * leveling immediately after G28.
  */
  //#define RESTORE_LEVELING_AFTER_G28
  //#define ENABLE_LEVELING_AFTER_G28
  ```

  to 

  ```
  //#define AUTO_BED_LEVELING_3POINT
  //#define AUTO_BED_LEVELING_LINEAR
  //#define AUTO_BED_LEVELING_BILINEAR
  #define AUTO_BED_LEVELING_UBL     --> Remove //
  //#define MESH_BED_LEVELING

  /**
  * Normally G28 leaves leveling disabled on completion. Enable one of
  * these options to restore the prior leveling state or to always enable
  * leveling immediately after G28.
  */
  #define RESTORE_LEVELING_AFTER_G28    --> Remove //
  //#define ENABLE_LEVELING_AFTER_G28
  ```
  
- Search for ```Unified Bed Leveling``` line(1937)
  Change line 1942 from ```#define MESH_INSET 1```
  to ```#define MESH_INSET 10```
  
  Change line 1943 from ```#define GRID_MAX_POINTS_X 10```  
  to ```#define GRID_MAX_POINTS_X 15```  
  Uncomment line 1954 by removing the ```//``` before ```#define UBL_MESH_WIZARD```  
  Uncomment line 1974 ```//#define LCD_BED_LEVELING```  
  Uncomment Line 1983 ```//#define LCD_BED_TRAMMING```  
  Uncomment Line 1990 ```//#define BED_TRAMMING_USE_PROBE```  
  Uncomment Line 2138 ```//#define EEPROM_INIT_NOW   // Init EEPROM on first boot after a new build```

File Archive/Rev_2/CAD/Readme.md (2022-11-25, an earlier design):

All supported Step and Fusion 360 files. Feel free to modify the parts, but please upload them as remix to Thingiverse :)

Original file link:
Ender 3 Step: https://github.com/Creality3DPrinting/Ender-3/tree/master/Ender-3%20Mechanical

# How to change the tolerances

There is an f3d file in the CAD folder. This file format is for Autodesk Fusion 360, a free CAD program for private users. You can use it to adjust the tolerances if the STL files I provided do not fit.
As described in the tolerance test, there are different tolerances for vertical and horizontal holes. Follow the steps below to create your own STL.

## 1: Open the fusion file
First you have upload the file to fusion. Simply double click on the file or upload it to the browser in fusion on the left side (once you opended a folder e.g `My First Project` theres a small blue upload option at the very top). Then open the file, it should look close to this:

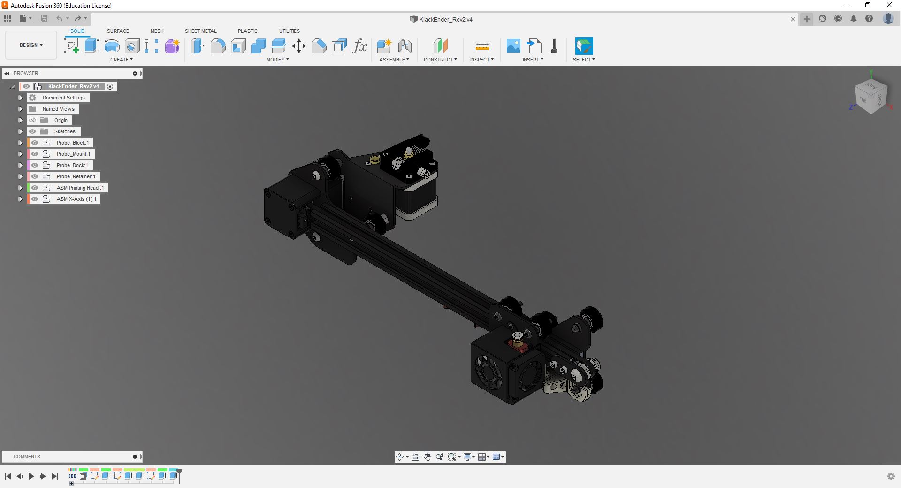
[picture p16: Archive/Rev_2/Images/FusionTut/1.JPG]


## 2: Open the parameters tab

Click on the `MODIFY`dropdown and select the parameters option.

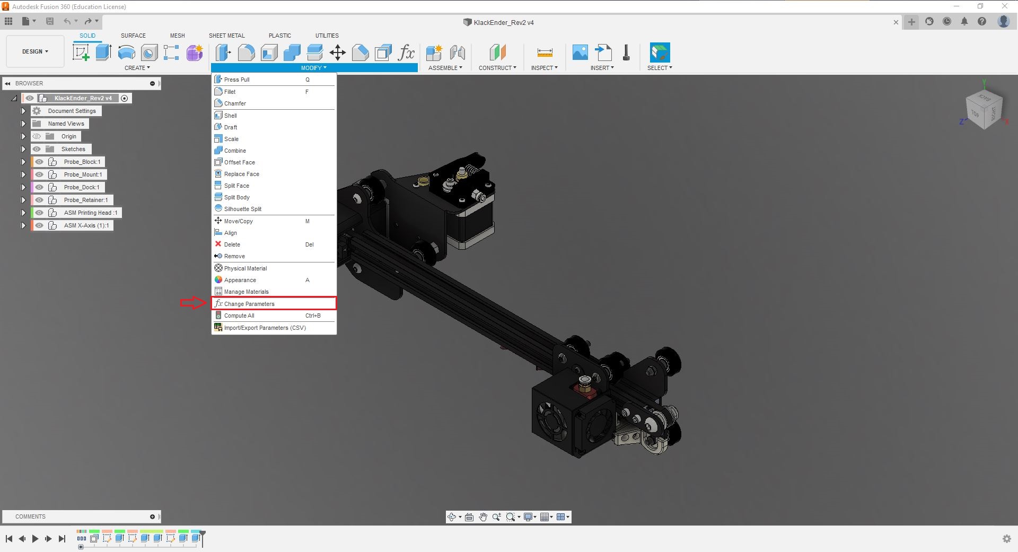
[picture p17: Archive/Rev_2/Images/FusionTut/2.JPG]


## 3: Change the parameters

Double click on the value you want to change.

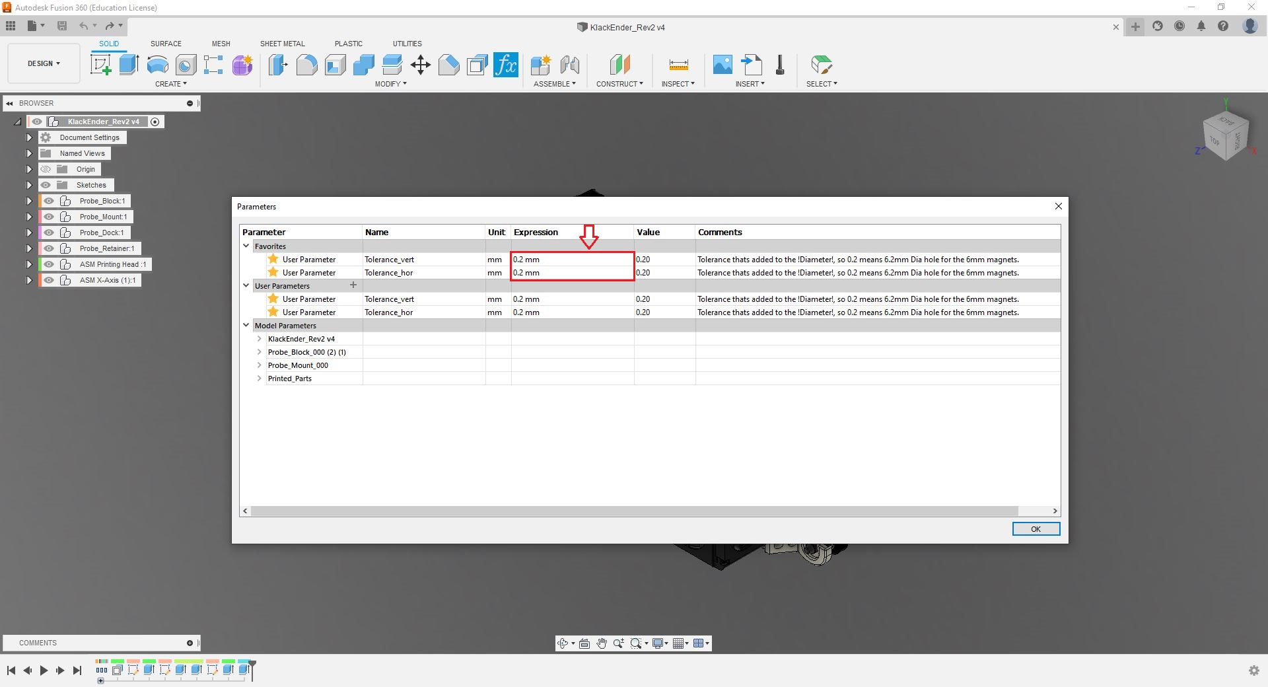
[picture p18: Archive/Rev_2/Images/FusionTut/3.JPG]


## 4: Find the file you want to export

Find the file you want to export in the browser on the left side. You can expand the folders by clicking on the small triangles. (You can also double click on the file in the CAD window, right click on it and select `Find In Browser`at the very end of the menu).

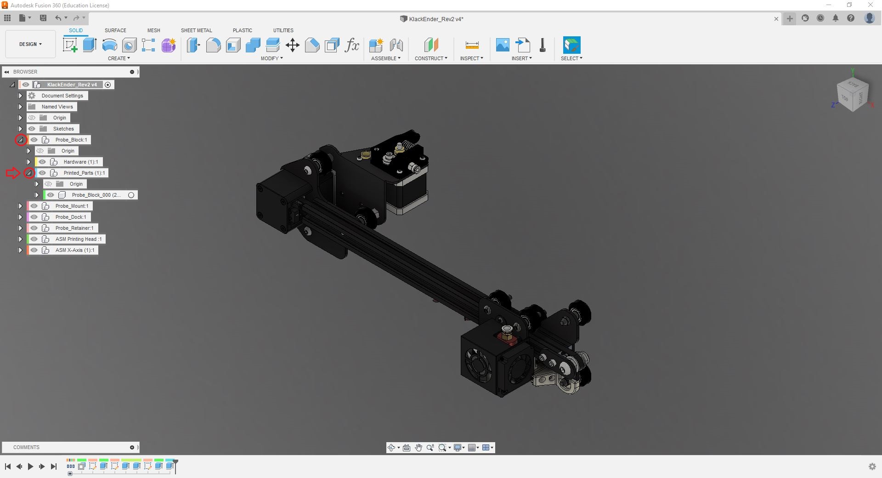
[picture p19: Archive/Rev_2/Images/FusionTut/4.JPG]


## 5: Export the STL

Once you found the file you want to export, right click on it and select `Save As Mesh`.

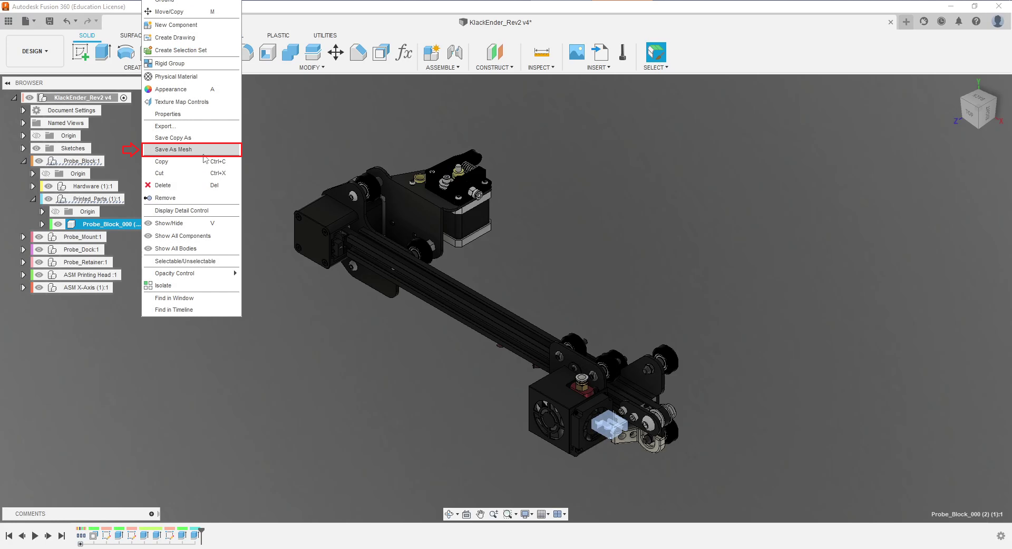
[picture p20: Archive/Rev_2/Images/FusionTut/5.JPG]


## 6: Save the STL

Simply confirm the small dialog on the right by clicking `OK`. Select a place on you PC to save it, that's all :)

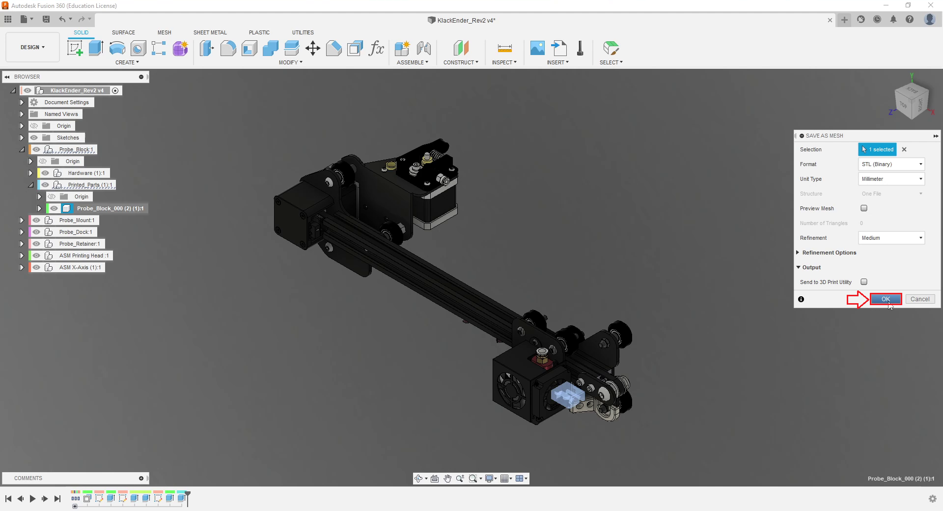
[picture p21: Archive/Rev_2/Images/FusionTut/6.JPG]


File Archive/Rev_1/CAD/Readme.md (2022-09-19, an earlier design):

CAD Files. Feel free to modify the parts, but please upload them as remix to Thingiverse :)

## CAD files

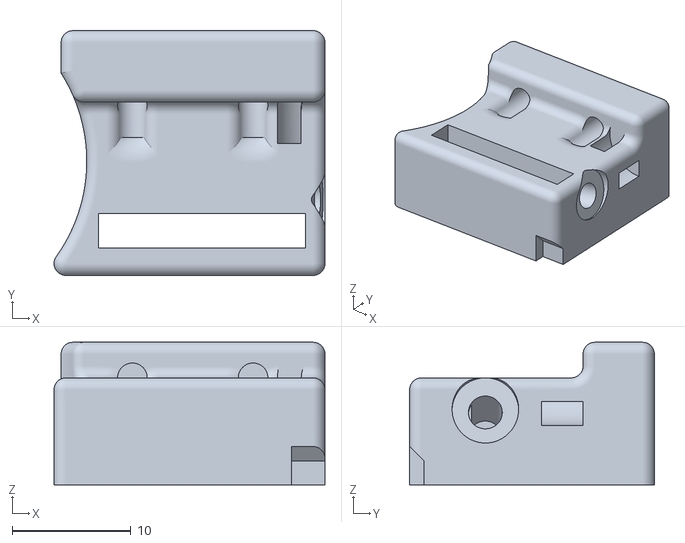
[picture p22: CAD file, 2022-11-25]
_ignore/Tolerances/v0.30/h0.00/Probe_Mount v0.3 h0.0.stl
22.8 x 20.6 x 12.0

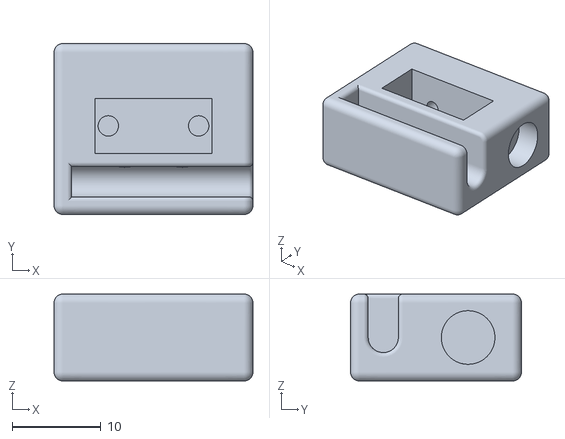
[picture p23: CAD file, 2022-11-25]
_ignore/Tolerances/v0.30/h0.05/Probe_Block v0.3 h0.05.stl
22.5 x 19.3 x 9.80

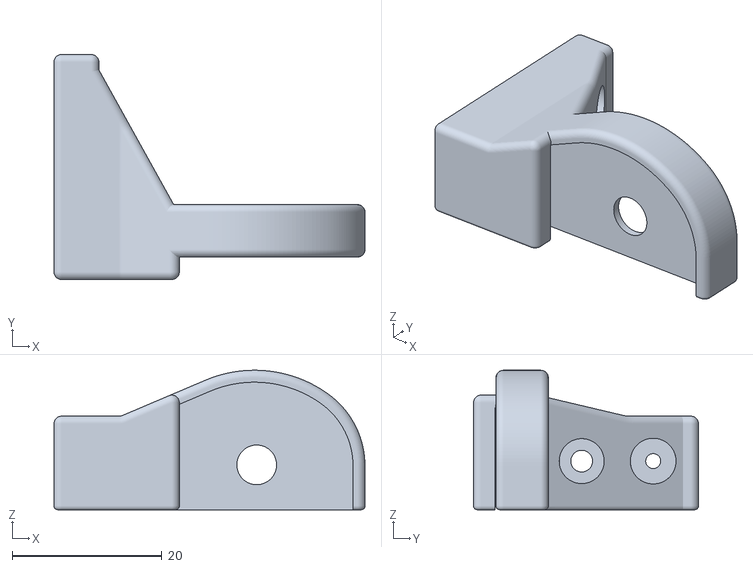
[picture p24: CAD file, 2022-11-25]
_ignore/Tolerances/v0.30/h0.10/Probe_Dock v0.3 h0.1.stl
41.5 x 30.1 x 18.6

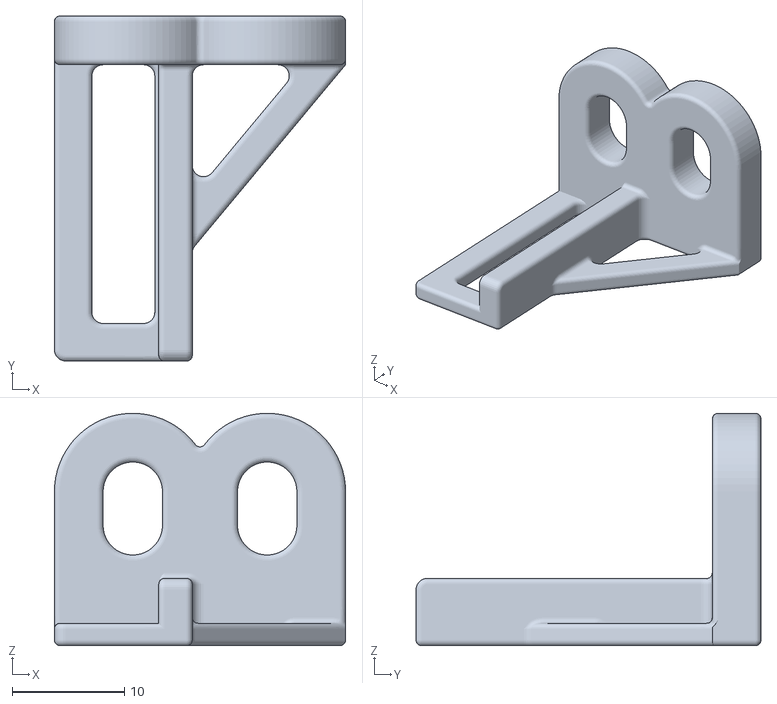
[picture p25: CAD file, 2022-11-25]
_ignore/Tolerances/v0.30/h0.20/Probe_Retainer.stl
26.0 x 30.8 x 20.7

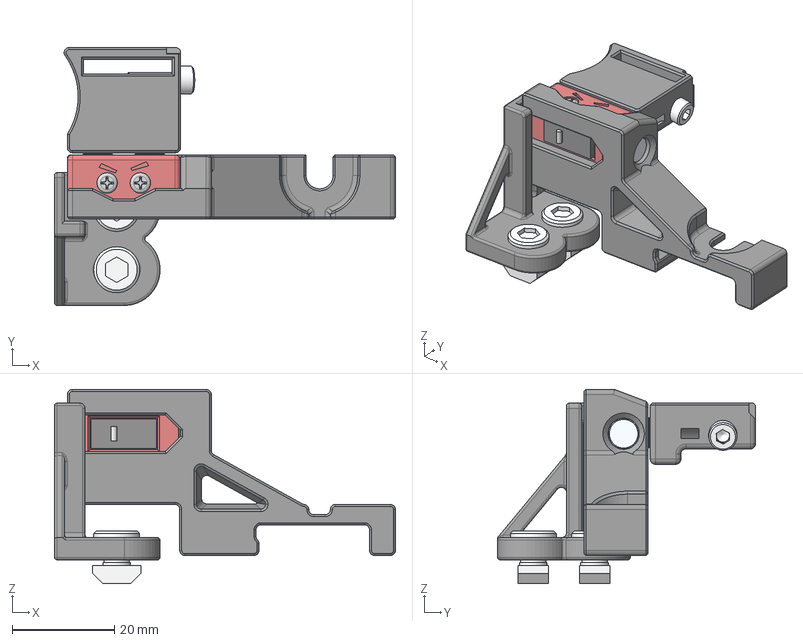
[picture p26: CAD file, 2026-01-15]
Beta/R2.2b/CAD/KlackEnder_Rev2.2b.step
66.7 x 50.5 x 38.0 mm
M3X10 SHCS v1
6x3mm Magnet v1 (2) x 2
Omron_D2F_F v1
94209A345_Thread-Forming Screws for Soft Metal x 2
6x3mm Magnet v1 (1) x 3
6x3mm Magnet v1
M5 T-Nut x 2

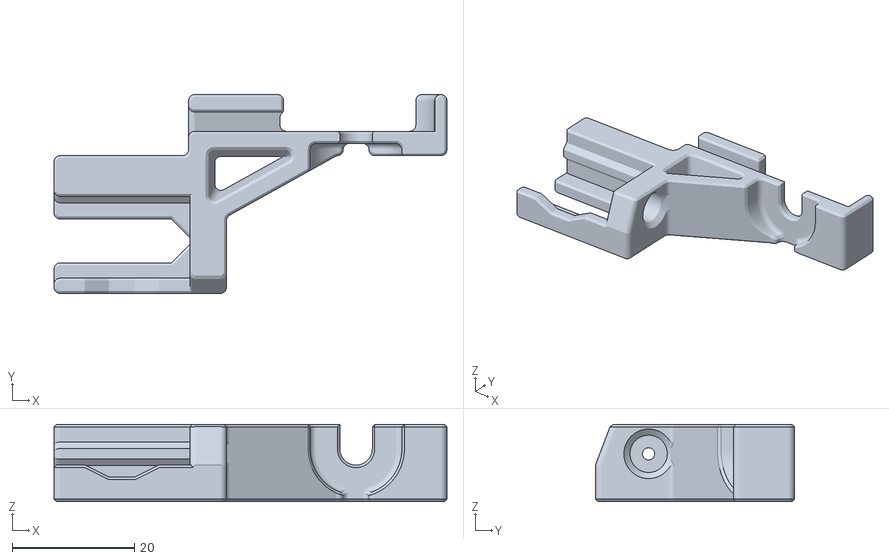
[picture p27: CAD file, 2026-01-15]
Beta/R2.2b/STLs/Probe_Dock.stl
64.2 x 32.5 x 12.6

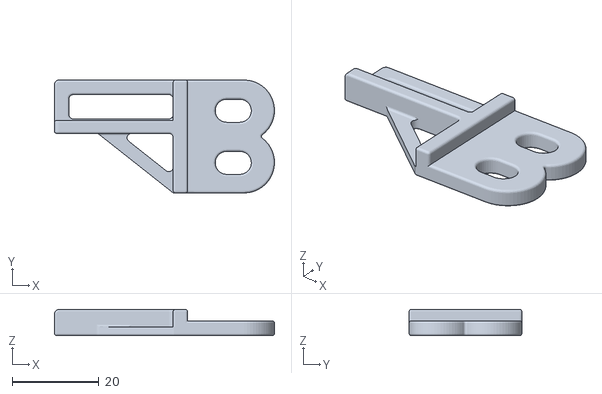
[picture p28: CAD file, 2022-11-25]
STL/Ender 3 S1/Probe_Retainer_S1.stl
50.7 x 26.0 x 6.00

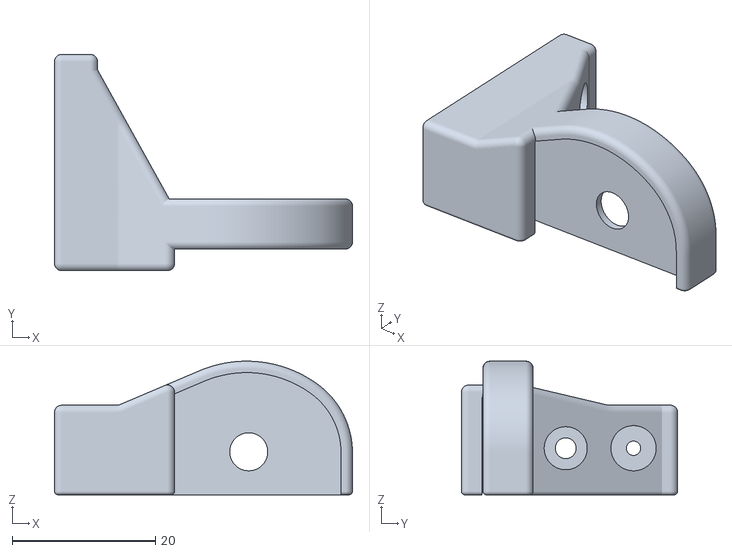
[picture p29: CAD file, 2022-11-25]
_ignore/Tolerances/v0.30/h0.30/Probe_Dock v0.3 h0.3.stl
41.5 x 30.1 x 18.6

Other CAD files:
_ignore/Tolerances/v0.30/h0.15/Probe_Mount v0.3 h0.15.stl
_ignore/Tolerances/v0.30/h0.30/Probe_Block v0.3 h0.3.stl
STL/Probe_Block v0.2 h0.2.stl
_ignore/Tolerances/v0.30/h0.00/Probe_Block v0.3 h0.0.stl
_ignore/Tolerances/v0.30/h0.05/Probe_Dock v0.3 h0.05.stl
_ignore/Tolerances/v0.30/h0.10/Probe_Mount v0.3 h0.1.stl
_ignore/Tolerances/v0.30/h0.15/Probe_Dock v0.3 h0.15.stl
_ignore/Tolerances/v0.30/h0.20/Probe_Dock v0.3 h0.2.stl
_ignore/Tolerances/v0.30/h0.25/Probe_Mount v0.3 h0.25.stl
Archive/Rev_1/STL/Probe_Block_000.stl
Archive/Rev_1/STL/Probe_Block_005.stl
Archive/Rev_1/STL/Probe_Block_010.stl
Archive/Rev_1/STL/Probe_Block_015.stl
Archive/Rev_1/STL/Probe_Block_020.stl
Archive/Rev_1/STL/Probe_Block_025.stl
Archive/Rev_1/STL/Probe_Block_030.stl
Archive/Rev_1/STL/Probe_Block_035.stl
Archive/Rev_1/STL/Probe_Dock.stl
Archive/Rev_1/STL/Probe_Mount_000.stl
Archive/Rev_1/STL/Probe_Mount_005.stl
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

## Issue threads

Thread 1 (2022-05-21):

AUTO_BED_MESH and G29 tries to take the probe out first

almihnea, 2022-05-21:
The 2 macros mentioned in the title do PROBE_OUT and then PROBE_IN instead of PROBE_IN and afterwards PRORBE_OUT
//
for the klipper config

kevinakasam, 2022-05-21:
That's completely correct. First the probe has to get out on the head and than back in into the dock.

almihnea, 2022-05-21:
Actually I think the probe in and probe out macros have their code switched. The probe in code shouldn't try to move to the left. It should only move to the probe, down and up.

Closed 2022-05-25.

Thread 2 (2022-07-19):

Marlin

probonopd, 2022-07-19:
Hello, this looks pretty genius. I especially like that you don't need to rewire the motherboard but can use the existing endstop cable (and possibly re-use the existing endstop switch?).

> A kind user (Farva) on my [Discord](https://discord.gg/xqpKrxt9FC) figured out how to configure Marlin for the Rev2. I had no time to test it yet. Feel free to join my server and test it out on your own. Once I tested it, I will upload detailed instruction here.

Is there any update on this? Could you post/link to that firmware configuration please?
Thanks, and keep up the great work.

kevinakasam, 2022-07-19:
Hey and thanks!
I just finished my exams last week and now I'm trying to work on all the request I got over the last months. This is also on my To-Do list. I still had no time to test the marlin config, but you can join my Discord and you will get some help with that :)

Farva42, 2022-07-21:
The Read me files for both Rev 1 & Rev 2 have been updated to include the recent changes to Marlin to better support this type of probe. I'll be working to include config files in the next little bit. If you have any issues I'm on discord regularly and can help.

probonopd, 2022-07-22:
Thank you very much. So nice to see this included in upstream Marlin.

What is the CODE needed to deploy the magnetic probe, do 9-point autoleveling, and put the magnetic probe back before starting the actual printing?

Farva42, 2022-07-22:
Start g-code would be
G29 L0; load mesh saved in slot 0.
G29 J3; probe 9 points and tilt loaded mesh.

Before you print you will want to create your mesh. You can find the option in the menus under motion UBL tools.
The probe will be automatically deployed any time there is a G29 command to probe as well as any time you ask it to home z if using rev 2.

Closed 2022-07-21.

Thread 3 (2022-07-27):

Automatic Z Calibration

genericapplesauce, 2022-07-27:
What would it take to get Automatic Z Calibration on an Ender 3? i.e. https://github.com/protoloft/klipper_z_calibration

The Vorons have a trigger they push with the nozzle, I'm assuming that won't work without modifying the Ender's left gantry bracket hitting the z stop?

Big fan of your work, Thanks!

kevinakasam, 2022-10-28:
Wanna use this comment to say that this in the making and runs as Beta on my Discord :)

Closed 2023-12-31.

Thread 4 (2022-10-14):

REV_2 Still Uses Z_MIN_PROBE pin in Marlin

daniel-walker, 2022-10-14:
On reviewing the Marlin code it appears to use the Z_MIN_PROBE pin for probing with little other options.

https://github.com/MarlinFirmware/Marlin/blob/bugfix-2.1.x/Marlin/src/module/probe.cpp#L611

In the REV_2 README I don't see you resetting the Z_MIN_PROBE to use the Z_STOP_PIN. It appears without doing this then REV_2 for Marlin would continue to use the Z_MIN_PROBE which is what REV_1 uses.

I think to change this some redefining in the Configuration.h would be needed, but the README doesn't mention it.

daniel-walker, 2022-10-21:
Z_MIN_PROBE_USES_Z_MIN_ENDSTOP_PIN

that seems to made this work.

Closed 2022-10-21.

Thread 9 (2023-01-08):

Probe mount doesn't fit to Ender 3S1

neshami, 2023-01-08:
Probe mount from STL folder doesn’t fit to Ender 3S1. Horizontal opening on probe mount which is included is 17.1mm and tab on 3S1 carriage is 19.6 mm wide and 3mm in height.
Can You include mount for Ender 3S1 to measures and include in 3S1 folder?

neshami, 2023-01-08:
Can You add that file HarryPulvirenti uploaded last for probe mount for 3S1? That file solved problem.

AustinTylerDean, 2023-05-01:
I would like whatever Harry made as well. I have to grind down the side, and after a few months I'm having problems with open circuits due to the slop in the probe mount.

Closed 2023-12-31.

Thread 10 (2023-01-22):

[Klipper] z_tilt z_positions needs exactly 1 items

cablesky, 2023-01-22:
I copied the exact configuration for Klipper. Unfortunately, the error message appears: "z_tilt z_positions needs exactly 1 items".
Can someone help me?

kevinakasam, 2023-02-17:
Just to answer this if anyone have the same problem: You have to remove the tilt z section if you dont have a dual z setup

Closed 2023-12-31.

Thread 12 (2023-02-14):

Probe_calibrate not working so well

ishay320, 2023-02-14:
i used this macro:
```
[gcode_macro calibrate_nozzle]
gcode:
  G28
  PROBE_OUT
  G0 X117 Y117 # the center of print bed
  Probe_calibrate
  PROBE_IN
```

it does good on `G28` and on `probe_out`, when it get to probe calibrate it starts good but when it returns the probe it move to x0 y-8.
there is a reasen to move it to 0 0 on `probe_in`?

ishay320, 2023-02-14:
the fix that i have got is:
```
[gcode_macro calibrate_nozzle]
gcode:
  G28
  PROBE_OUT
  G0 X117 Y117 # the center of print bed
  Probe_calibrate
```
and removing the probe manually

kevinakasam, 2023-02-17:
> there is a reasen to move it to 0 0 on probe_in?

Yes because after the probe got stored the print may start and starting at the zero position might help with other macros you use for a purgeline or so

Closed 2023-12-31.

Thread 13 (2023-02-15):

bed mesh macro

ishay320, 2023-02-15:
better macro for bed mesh:
```
[gcode_macro BED_MESH_CALIBRATE]
rename_existing: _BED_MESH_CALIBRATE
description: Perform Mesh Bed Leveling with klicky automount
gcode:
	G90
    PROBE_OUT

    _BED_MESH_CALIBRATE {% for p in params
           %}{'%s=%s ' % (p, params[p])}{%
          endfor %}

    PROBE_IN
```

it works with the original bed mesh button

DasBurninator, 2023-02-16:
Its not just the bed mesh macro that has this issue that could be easily resolved. It is all of the macros. z_tilt has this issue as well.

I suggest using the klickyprobe macros instead. Much better written.

kevinakasam, 2023-02-17:
Thanks for the comment! Yes you're right renaming the existing macros makes the usage a little easier. I will give your macro a try when I'm back home and edit the Klackender.cfg.

oldcrazyeye, 2023-12-31:
No progress in this thread, closing

Closed 2023-12-31.

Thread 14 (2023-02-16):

[Feature Request] Use klickyprobe macros

DasBurninator, 2023-02-16:
Instead of using the macros included that aren’t really written well, utilize the existing work of the Klicky Probe macros.

This would allow for a much better user experience.

The existing macros could be updated to be much better if the `rename_existing:` function was utilized.

kevinakasam, 2023-02-17:
Hey!
There is something in the making to get the Klicky macros working with the Klack. Harry from my Discord spent some time to get all the changes done. I will link this in the instructions soon so you can chose if you want to use my very basic macros or the more advanced Klicky-Klack macros:

https://github.com/Harrypulvirenti/Klack-Probe-Macros

DasBurninator, 2023-02-21:
I ran a diff on all of this... Its just renamed macros and the addition of one to handle manual screw adjust. Also removed z-tilt adjust which is more useful than manual screw adjust for some people. Why not just provide steps for setting up klickyprobe macros? This seems like overkill and just another set of macros to maintain vs just providing the config parts needed in the variables file.

kevinakasam, 2023-06-19:
Hey @Ordspilleren That would be great!
Feel free to add a Klicky Macro adaption block to the readme and then do a pull request :) Would be happy to merge it then

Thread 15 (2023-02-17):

Missing a Critical Marlin Step In Readme (for CR/BL Touch users)

AustinTylerDean, 2023-02-17:
Critical for me at least! I migrated from a CR Touch, so I knew I had to comment out "BL Touch" but not having the change below really was a bummer!

(currently line 1280 in Configuration.h) #define Z_MIN_PROBE_USES_Z_MIN_ENDSTOP_PIN

If you are coming from a Hall Effect sensor, or many other sensors.... you have this commented out.

I'd throw together the two changes and a heading in the instructions for those poor souls that die a little inside every time their rig crashes into the bed.

Otherwise, even though I had to customize some stuffs to accommodate a Sprite Pro, this thing works! Can't wait to get it really fine tuned!

Closed 2023-03-19.

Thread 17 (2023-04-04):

[QUESTION] Unklicky...possibly?

StackingDeezLayers, 2023-04-04:
Hello. I would like to know if you are working on a version to support the superior Unklicky. It uses magnets instead of a micro switch which causes for better accuracy. I am going to be using this on my Voron, so I would like a shared ecosystem. Thank you in advance!

StackingDeezLayers, 2023-04-22:
Re-opend because I still think this is possible. I got it mostly working. I will add a pull request once finished

Closed 2023-05-29.

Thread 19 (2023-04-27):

Cut Vent Ring for Ender 3

lanotlab, 2023-04-27:
I'm upgrading my ender 3 v1 with the klackender probe, but my vent ring was too big.
I've altered it so it can now be used with the probe
[cut vent ring.zip](https://github.com/kevinakasam/KlackEnder-Probe/files/11347471/cut.vent.ring.zip)

Closed 2023-12-31.

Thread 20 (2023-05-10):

Move out of range while redocking probe.

orangemn6, 2023-05-10:
Hey! Just installed this onto my ender 3, and I am encountering this error while starting a print:

```Move out of range: 245.000 -8.000 20.000 [0.000]```

I can upload my printer.cfg below:

[printer.cfg.txt](https://github.com/kevinakasam/KlackEnder-Probe/files/11445819/printer.cfg.txt)

Thanks!

orangemn6, 2023-05-10:
Fixed! I forgot to read the docs, my y `min_position` was not set to -8. Thanks for this amazing project!

Closed 2023-05-10.

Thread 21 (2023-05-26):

Ender 5 support?

qwertychouskie, 2023-05-26:
At the lab, we have an Ender 3, and Ender 3 Pro, and an Ender 5 Pro.  Would be nice to be able to use this on all 3 printers :)

I imagine the part that goes on the toolhead would be identical, but the part that mounts to the frame would be a bit different, and probably the load/upload sequences would have to be tweaked too.

oldcrazyeye, 2023-12-31:
Nothing in the works for ender 5 currently. Files are parametric so feel free to give it a shot in cad.

Closed 2023-12-31.

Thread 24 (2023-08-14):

Please help Klackender Config issue

iiiiiiiiddddddkkkkkkk, 2023-08-14:
I just set up the klackender config and i got this error from klipper any suggestions?

Section 'menu __main' is not a valid config section

Once the underlying issue is corrected, use the "RESTART"
command to reload the config and restart the host software.
Printer is halted

YungChin95, 2023-08-14:
Remove the bottom part of the config named "Klackender Menu"

iiiiiiiiddddddkkkkkkk, 2023-08-14:
ok i'll try that thanks for the rapid response

iiiiiiiiddddddkkkkkkk, 2023-08-14:
did that now i get this

Option 'points' is not valid in section 'homing_override'

Once the underlying issue is corrected, use the "RESTART"
command to reload the config and restart the host software.
Printer is halted

iiiiiiiiddddddkkkkkkk, 2023-08-14:
> Remove the bottom part of the config named "Klackender Menu"

I did that now I get this error

Option 'points' is not valid in section 'homing_override'

Once the underlying issue is corrected, use the "RESTART"
command to reload the config and restart the host software.
Printer is halted

iiiiiiiiddddddkkkkkkk, 2023-08-14:
never mind i forgot to comment out the stuff in z tilt

Closed 2023-12-31.

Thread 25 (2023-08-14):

Move out of range: 245.000 -8.000 20.000 [0.000]

iiiiiiiiddddddkkkkkkk, 2023-08-14:
I just attempted a print but I got this error

Move out of range: 245.000 -8.000 20.000 [0.000]

Closed 2023-08-15.

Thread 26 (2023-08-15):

When Homing I get this error  Endstop z still triggered after retract any ideas?

iiiiiiiiddddddkkkkkkk, 2023-08-15:

iiiiiiiiddddddkkkkkkk, 2023-08-15:
Even when the probe is removed I get this error

5drei1, 2024-01-29:
you found the reason?

Closed 2023-08-15.

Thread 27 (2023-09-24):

relative_reference_index in the bed_mesh section is deprecated

eduhoribe, 2023-09-24:
Klipper deprecated the `relative_reference_index` option for the `bed_mesh` in the version `20230619`, details on how to update the configuration are specified [here](https://www.klipper3d.org/Bed_Mesh.html#the-deprecated-relative_reference_index).

After a quick read, my two cents is that we could replace it with the `zero_reference_position` pointing to one of the bed leveling screws.

miroan81, 2023-09-30:
I've just updated to the newest version and this thing popped out. After looking and reading I decided just to comment RRI and leave it like that, did bed mesh few times nothing weird happened, I guess zero_reference_position is not actually needed if everything works ok

oldcrazyeye, 2023-12-31:
Updated in the config now, thank you

Closed 2023-12-31.

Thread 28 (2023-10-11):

"Probe triggered prior to movement" error randomly popped up when running AUTO_BED_MESH

AhambaliJ, 2023-10-11:
Hi all,

I'm making this issue to share my experience troubleshooting error mentioned and the solution, in case anyone is experiencing the same issue.
Just managed to installed the parts and get the probe to smoothly goes in and out of its dock.
Absolutely no problem when homing Z.
Tested manually attaching probe to trigger the probe on bed, and raising the head(Z) +1 at a time, probe gets open at sometimes at +1, other times at +3. I.e ranging from Z 0 to Z 3
This causes issues during calibrating bed mesh, specifically when taking multiple sample as the probe get stuck in "Triggered" status and which give me a clue that it needs to move upwards(+Z) more.

Solution:
Go into printer.cfg and scroll down to the [probe] section. Increase the value of "sample_retract_dist".
For me, I made the value as the same as my "z_offset" value.

Hope this helps someone.

kevinakasam, 2023-10-11:
Thanks for sharing :)

Closed 2023-10-11.

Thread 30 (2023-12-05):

Wiring an Ender3 S1 Pro issue

icemul1900, 2023-12-05:
I'm trying to wire the micro switch to the Ender3 S1 Pro and I'm not having any luck. I have been trying the "Z Limit Interface" but it's 3 prongs, so I've tried all the combos but none of them work.
How am I supposed to wire the Klack to the S1 Pro motherboard?

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

oldcrazyeye, 2023-12-31:
You should absolutely be able to use the z limit pins. Only use IO and GND and not 5v. Identify the pin mapping of the IO pin and add that to klipper config under `probe_pin`

Closed 2023-12-31.

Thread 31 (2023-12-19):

Code parsing errors

theprintingpress, 2023-12-19:
When I added the klackender config file, mainsail gave me this report:

Klipper reports: ERROR

Source contains parsing errors: '/home/biqu/printer_data/config/Klackender.cfg'
	[line 134]: 'PROBE_OUT\n'
	[line 135]: '_BED_MESH_CALIBRATE\n'
	[line 136]: 'PROBE_IN\n'

Once the underlying issue is corrected, use the "RESTART"
command to reload the config and restart the host software.
Printer is halted

theprintingpress, 2023-12-19:
I looked through the other issues and realized that I still had the code for dual z setups, as soon as I commented that code, it started working.

Closed 2023-12-19.

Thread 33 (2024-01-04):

Z_TILT_ADJUST issue

mlee12382, 2024-01-04:
The Z_TILT_ADJUST macro needs to call _Z_TILT_ADJUST instead of Z_TILT_ADJUST otherwise it becomes a recursive call.

Also the example config should include a SCREWS_TILT_CALCULATE macro.

DMNerd, 2024-01-04:
I made a pull request for SCREWS_TILT_CALCULATE macro

mlee12382, 2024-01-04:
> I made a pull request for SCREWS_TILT_CALCULATE macro

Awesome, I might have done it when I got home from work, but if you've already done it, then I won't worry about it :)

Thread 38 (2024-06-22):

HELP

yagoporto, 2024-06-22:
Good morning! I need your help, I did the entire installation of klackEnder, everything works normally, but when the switch is activated the nozzle continues to descend, it seems that it is not regular, I have already done the test with a multimeter and everything is working.

I'm making an Ender 3 S1.

Follow my configuration file.

I didn't quite understand how to configure the "pin" in the probe part.

[probe]
pin: PA8 #Change to where you plug your probe in, endstop or probe pin pulled high (^)
z_offset: 0 #Measure per your specific setup
x_offset: 4 # negative = left of the nozzle
y_offset: 21 # negative = in front of of the nozzle
speed: 5.0
lift_speed: 15.0
sample_retract_dist: 1
samples: 2
samples_tolerance_retries: 6

The pin is correct?

Walkb4uRoll, 2024-07-03:
hey boss could you help compile for a ender 3 v2?

j0e57, 2024-08-15:
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

I just try to help pin is where you attach your klackender cable.. its depend on your mainboard layout, if you use stock (maybe Creality 4.22 or 4.27 board) or other like SKR 1.3 1.4 SKR mini etc, its all use different pin for Z probe
According to https://github.com/MarlinFirmware/Marlin/blob/2.0.x/Marlin/src/pins/stm32f1/pins_CREALITY_V4.h
Z probe pin is PA7 :) thats why nozzle continue to descend :)

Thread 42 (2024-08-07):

When homing Z: Endstop z still triggered after retract

1knueller, 2024-08-07:
When homing Z i get this error message:

!! Endstop z still triggered after retract

I have an Ender 3 Pro with SKR Mini v2
(https://github.com/bigtreetech/BIGTREETECH-SKR-mini-E3/blob/master/hardware/BTT%20SKR%20MINI%20E3%20V2.0/Hardware/BTT%20SKR%20MINI%20E3%20V2.0-PIN.pdf)

In the cfg I have this:

[probe]
pin: ^PC2

That is Z-Endstop (makes sense since i used touch probe as z endstop aswell)

1knueller, 2024-08-07:
So I started posting and wanted to clarify everything for the post but I resolved the issue.
The situation was that one of the switch pins did not have contact with the magnet.

Checking continuity with a multimeter (as recommended in the buildinstructions) I could find the issue. Magnet to magnet, and that one magnet to the other pin did not work.

(I have printed it with a dlp printer it has such good tolerance/precision that the default clearance is way too much and the pins are not pressed against the magnet fully. I also used a tiny bit of glue for the magnet and maybe some of that got stuck between pin and magnet)

Closed 2024-08-07.

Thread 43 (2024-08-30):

Magnet keeps falling out of Mount

JonasV328, 2024-08-30:
Hello!

I have printed and used about 10 iteratations of the Probe_Mount in different tolerance combinations. I have always used the tolerance test print at first. Using PETG with press fitting magnets, due to being close to the hotend permanently, it kept getting soft and losing the magnets.
Now I have switched to ASA which is heat resistant but has low flexibility and low layer adhesion, so press fitting the magnets is not possible as the mount splits along the layers if you try to press in the magnet. I could only use tolerance settings with easy to insert magnets with super glue but the magnets still fall out after a handful of prints.

What glue do you use? How do you manage to keep the Probe_Mount in working condition?

I am really thrilled by this great leveling setup and all other parts work perfectly, only Probe_Mount keeps falling apart.

Thank you!

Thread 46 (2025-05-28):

Dock & Mount for Voxelab Aquila C2

pi-squared-studio, 2025-05-28:
The implementation of this project is laid out here for Voxelab Aquila C2.
In theory, it is also suitable for the standard Ender 3, since the mounting dimensions do not differ much.

One of the features of this edition is:
- Lowering the sensor contact level by 5 mm. Now you can easily use a wide range of nozzles without dismantling, both standard (MK8, V6) and with increased height (V3, KE, K1 Max, Neptune 4, Budaschnozzle Airbrush...)
- Additional wire outlet on the front side, for cable management. Invisible behind the carriage.
- a special recess for the wires to contact the magnet, a through hole so that the wires do not accumulate in the node under the magnet, an annular platform under the magnet so that it protrudes 0.1 mm.

[KlackEnder_Probe_for_Aquila.zip](https://github.com/user-attachments/files/20495756/KlackEnder_Probe_for_Aquila.zip)

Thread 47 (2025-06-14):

Changing magnet dimensions parameters causes errors and issues in Fusion360

rlesac, 2025-06-14:
I was very glad to see a parametric F3D design and wanted to change the parameters of the magnets, as I don't have 6x3mm at hand.
Well no luck there.
Tried 4x4mm and get a load of errors and geometry falls apart.
10x2mm even worse.

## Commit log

2022-07-21 Update Marlin support
2022-07-21 Remove old Marlin info
2022-09-19 Clean up
    [KlackEnder.cfg, KlackEnderRev2.cfg, Probe_Block.stl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]
2022-09-30 Set the preset z_offset to 0
    [KlackEnderRev2.cfg]
2022-11-25 Rev2.1 Release
    Update of the KlackEnder to Rev2.1.
    [KlackEnder.cfg, KlackEnderRev2.cfg, Probe_Block v0.0 h0.0.stl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]
2023-02-09 Added missing Probe_Retainer.stl to zips
    [Probe_Retainer.stl]
2023-02-10 Change instruction to match comment on Marlin bugfix-2.1.x*
    https://github.com/MarlinFirmware/Marlin/blob/bugfix-2.1.x/Marlin/Configuration.h#L1748
2023-02-10 Fixed formatting for the Unified Bed Leveling section
2023-03-19 Update README.md
    Fix confusion with pin defines & remove line numbers to avoid issues.
2023-04-01 Update README.md
    Fix Marlin probe stow
2023-04-18 updated klipper instructions
2023-11-29 Klipper cfg update
    [KlackEnderRev2.cfg]
2023-12-31 Update KlackEnderRev2.cfg
    Remove deprecated Relative_reference_index in favor of zero_reference_position. Updated the homing_override to allow individual axis homing
    [KlackEnderRev2.cfg]
2023-12-31 Fixed the macro being called in the screen menu.
    The previous command was AUTO_BED_MESH, but the correct marco is BED_MESH_CALIBRATE with the new update. So that's fixed now.
    [KlackEnderRev2.cfg]
2024-05-01 Update README.md
    Edit Probe pin for less confusion
2024-08-31 Update README.md
    Reduce default speeds from 333mm/s to 200mm/s
2024-08-31 Update KlackEnderRev2.cfg
    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
    [KlackEnderRev2.cfg]
2024-09-26 cfg cleanup
    Adjusted the config changes to be a little more clear on what a user needs to change as well as adjusting points for probe offsets where needed. Should hopefully save users (and us) some headaches. R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
    [KlackEnderRev2.cfg]
2024-09-26 Fixed typo and STC
    Fixed a typo and added in SCREWS_TILT_ADJUST
    [KlackEnderRev2.cfg]
2024-11-02 Fixed improper indents
    [KlackEnderRev2.cfg]
2026-01-15 Added beta. Separated cfg and macros
    [AddToPrinter.cfg, KlackEnder.cfg, KlackEnderRev2.cfg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]
